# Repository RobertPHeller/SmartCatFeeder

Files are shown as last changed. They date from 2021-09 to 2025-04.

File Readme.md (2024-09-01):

# Smart Cat Feeder

A smart cat feeder, an "upgrade" from the [feeder on
Thingiverse.com](https://www.thingiverse.com/thing:8175), using an ESP32-S3
Dev board -- a more powerful processor. It will have a touch screen, and
provide a web server over WiFi. It will use a load cell to measure how full
the food bowl is, it will have a sensor to check when the food bin is low and
have a battery backup to operate in the event of a power failure, to insure
your cat will be fed when the power goes out.

[Adafruit Parts List](http://www.adafruit.com/wishlists/595396)
- [Adafruit TFT FeatherWing - 3.5" 480x320 Touchscreen for Feathers - V2 with TSC2007](https://www.adafruit.com/product/3651)
- [DC Motor + Stepper FeatherWing Add-on For All Feather Boards](https://www.adafruit.com/product/2927)
- [Adafruit VL6180X Time of Flight Distance Ranging Sensor (VL6180) - STEMMA QT](https://www.adafruit.com/product/3316)
- [Adafruit NAU7802 24-Bit ADC - STEMMA QT / Qwiic](https://www.adafruit.com/product/4538)
- [Adafruit PCF8523 Real Time Clock Breakout Board - STEMMA QT / Qwiic](https://www.adafruit.com/product/5189)
- [Strain Gauge Load Cell - 4 Wires - 1Kg](https://www.adafruit.com/product/4540)
- [Adafruit ESP32-S3 Feather with STEMMA QT / Qwiic - 8MB Flash No PSRAM](https://www.adafruit.com/product/5323)
- 2x [STEMMA QT / Qwiic JST SH 4-Pin Cable - 50mm Long](https://www.adafruit.com/product/4399)
- [STEMMA QT / Qwiic JST SH 4-pin Cable - 100mm Long](https://www.adafruit.com/product/4210)
- [Woven USB Cable with USB Type A to Right Angle USB Type C - Black 1 meter long](https://www.adafruit.com/product/5031)

DF Robot Parts list
- 2x [Turbo Metal Gear Worm Motor (12V 40RPM 8kg.cm)](https://www.dfrobot.com/product-1484.html)

Amazon Parts list
- [Van Ness Pets Lightweight Stainless Steel Cat Bowl, 8 OZ Food And Water Dish, Natural](https://www.amazon.com/Van-Ness-Lightweight-Dish-8-Ounce/dp/B00LM90GJI/)

Woodpeckers Crafts Parts List
- [1/8" x 24" x 48" Baltic Birch Sheets B/BB](https://woodpeckerscrafts.com/1-8-x-24-x-48-baltic-birch-sheets-b-bb/)
- 2x [1/4" x 12" Dowel](https://woodpeckerscrafts.com/1-4-x-12-dowel/)
- [1/2" x 12" Dowel Rod](https://woodpeckerscrafts.com/1-2-x-12-dowel-rod/)

Misc hardware
- 10 M3x6mm Allen head
- 7  M4x6mm Allen head
- 4  M6x12mm Allen head
- 4  M6 nuts
- 12 M2.5x6 flat head (counter sunk)
- 4  M2.5x12 flat head (counter sunk)
- 16 M2.5 nuts
- 4  M2.5x4 spacers
- 6  6-32x3/4" round head
- 7  6-32 nuts
- 4  #6x1/4 spacers (one metal, 3 plastic)
- small hinges
- magnetic cabinate door latch

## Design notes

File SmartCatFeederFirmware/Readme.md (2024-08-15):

# Smart Cat Feeder Firmware

Code for the Adafruit ESP32S3 Feather

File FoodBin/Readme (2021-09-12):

FreeCAD Python Scripts for the feed bin and framework.  Panels to be laser cut
from 1/8" plywood.

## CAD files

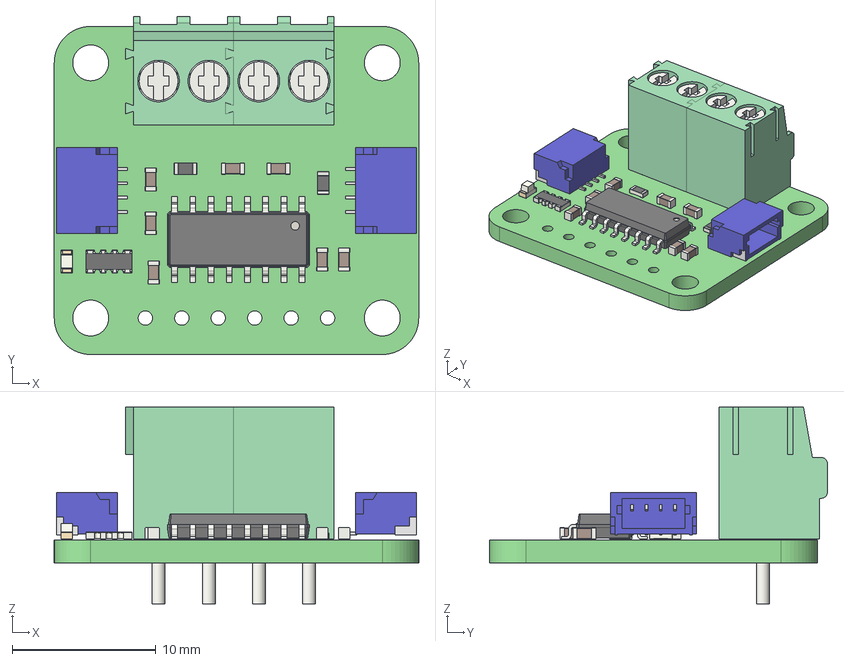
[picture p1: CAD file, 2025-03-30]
FoodBin/AdafruitNAU7802.step
25.4 x 23.6 x 13.7 mm
Adafruit NAU7802 Breakout PCB

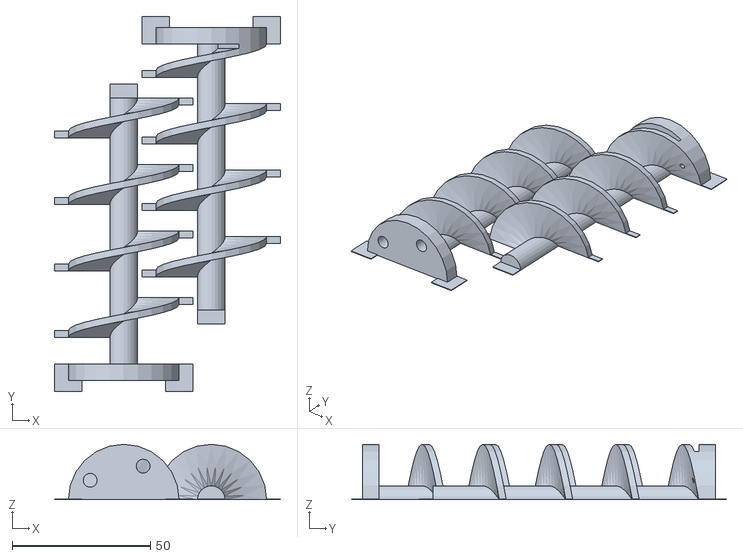
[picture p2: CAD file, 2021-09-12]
Auger_Drive_Screw_Conveyor/AugerWithCurlFlash.stl
81.6 x 135.4 x 20.0

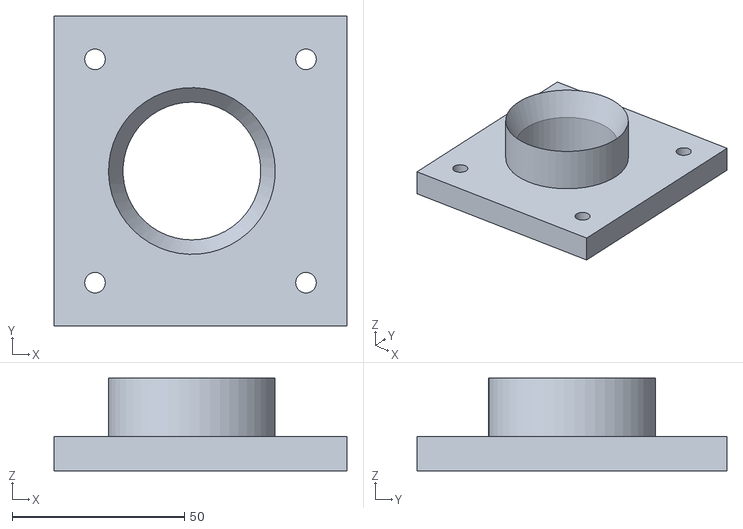
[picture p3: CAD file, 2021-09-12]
Auger_Drive_Screw_Conveyor/AugerMount.stl
85.0 x 90.0 x 27.0

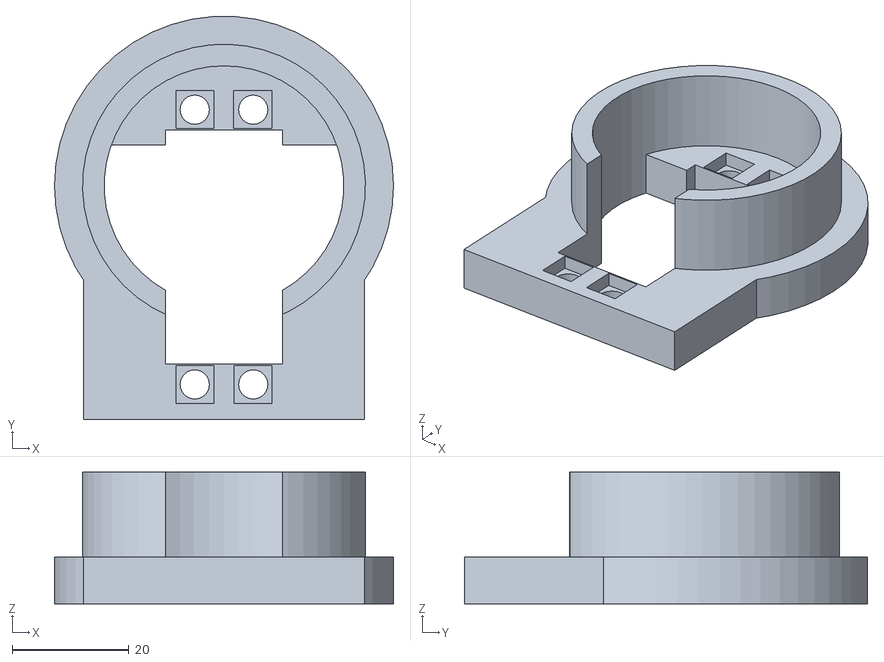
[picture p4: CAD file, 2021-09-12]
Auger_Drive_Screw_Conveyor/ServoMount.stl
58.0 x 68.9 x 22.5

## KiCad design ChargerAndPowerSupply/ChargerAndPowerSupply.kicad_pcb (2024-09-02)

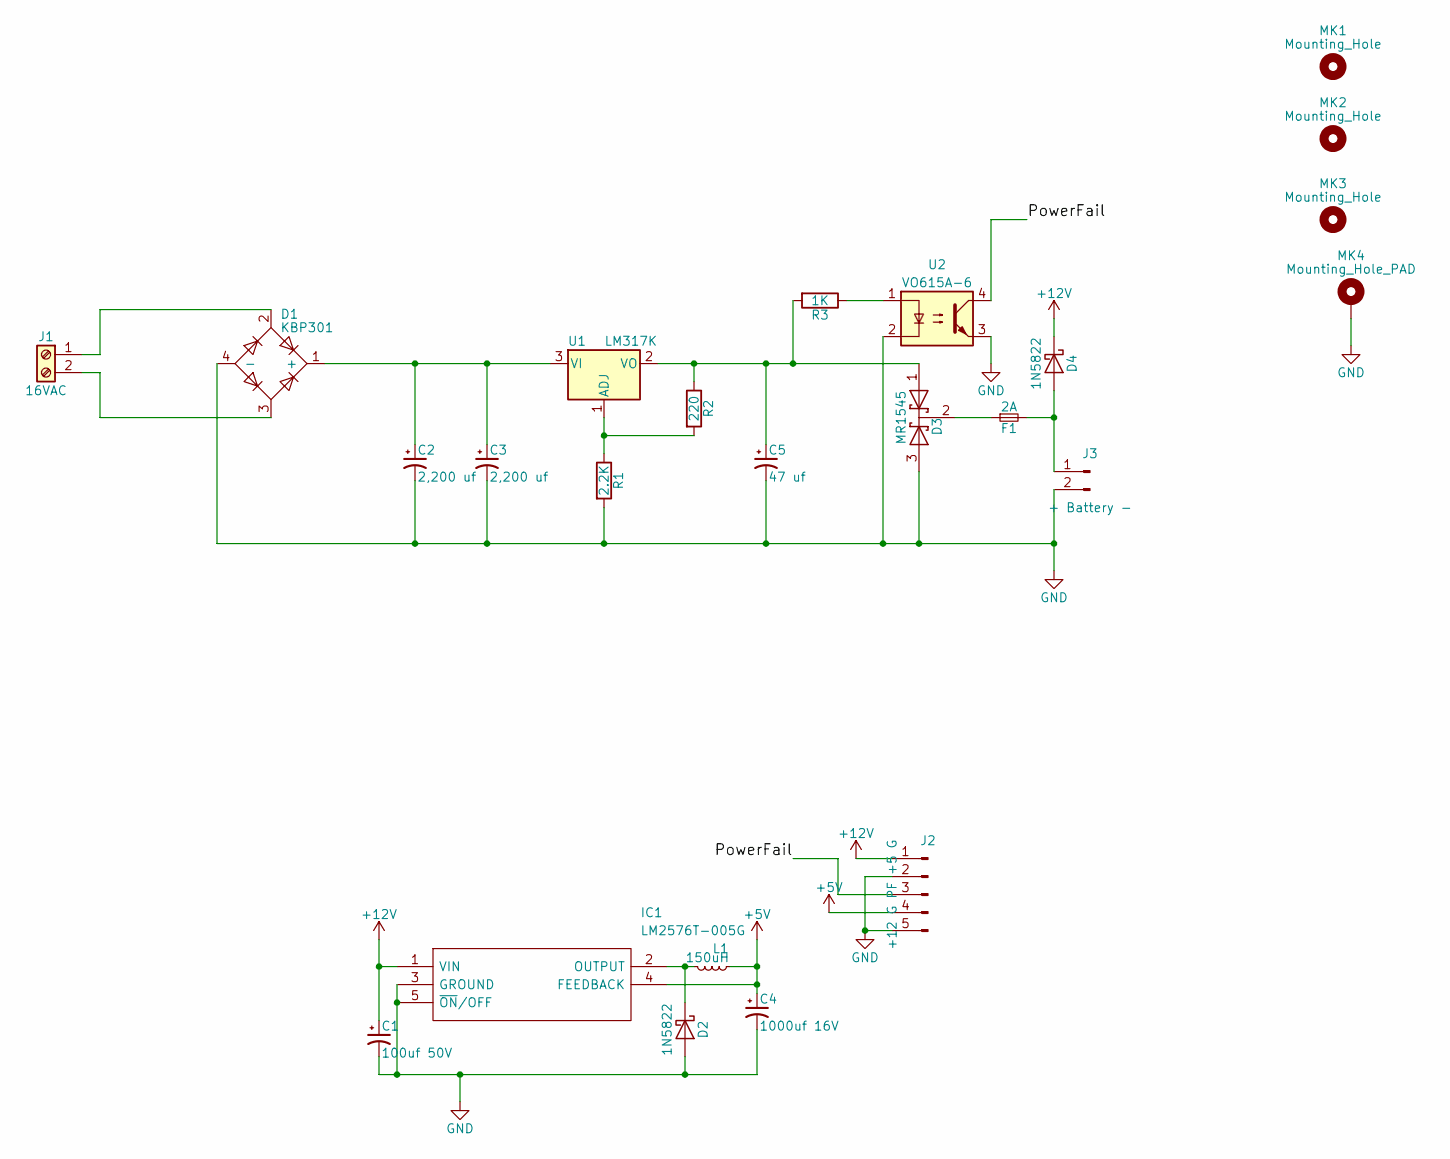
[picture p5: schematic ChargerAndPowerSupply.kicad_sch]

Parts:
C1: 100uf 50V; CP_Radial_D8.0mm_P5.00mm; Mouser Part Number 667-EEU-FR1H101B
C2, C3: 2,200 uf; CP_Radial_D16.0mm_P7.50mm; Mouser Part Number 140-REA222M1HBK1636P
C4: 1000uf 16V; CP_Radial_D10.0mm_P5.00mm; Mouser Part Number 667-EEU-FR1C102
C5: 47 uf; CP_Radial_D6.3mm_P2.50mm; Mouser Part Number 140-REA470M1HBK0611P
D1: KBP301; KBP301G; Mouser Part Number 905-KBP301
D2, D4: 1N5822; D_DO-201AD_P15.24mm_Horizontal
D3: MR1545; TO-220_Vertical
F1: 2A; MRT2; Mouser Part Number 530-MRT2
IC1: LM2576T-005G; TO-220-5_Pentawatt_Multiwatt-5_Vertical_StaggeredType1; Mouser2 Part Number 863-LM2576T-005G
J1: 16VAC; TerminalBlock_Pheonix_MKDS1.5-2pol; Mouser Part Numer 651-1017491
J2: +12 G PF +5 G; 26607050
J3: + Battery -; 26607020
L1: 150uH; L_Toroid_Vertical_L24.6mm_W15.5mm_P11.44mm_Pulse_KM-4; Mouser Part Number 673-PE-53113NL
MK1, MK2, MK3: Mounting_Hole; MountingHole_4.5mm
MK4: Mounting_Hole_PAD; MountingHole_4.5mm_Pad
R1: 2.2K; R_Axial_DIN0204_L3.6mm_D1.6mm_P7.62mm_Horizontal; Mouser Part Number 603-CFR-12JT-52-2K2
R2: 220; R_Axial_DIN0204_L3.6mm_D1.6mm_P7.62mm_Horizontal; Mouser Part Number 603-CFR-12JT-52-220R
R3: 1K; R_Axial_DIN0204_L3.6mm_D1.6mm_P7.62mm_Horizontal; Mouser Part Number 603-CFR-12JB-52-1K
U1: LM317K; TO-220_Vertical; Mouser Part Number LM317KCT
U2: VO615A-6; DIP-4_W7.62mm

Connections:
+5V: C4.1, IC1.4 (FEEDBACK), J2.4, L1.1
+12V: C1.1, D4.1 (K), IC1.1 (VIN), J2.1
/PowerFail: J2.3, U2.4
GND: C1.2, C2.2, C3.2, C4.2, C5.2, D1.4 (-), D2.2 (A), D3.3 (A), IC1.3 (GROUND), IC1.5 (~ON/OFF), J2.2, J2.5, J3.2, MK4.1, R1.2, U2.2, U2.3
unnamed: C2.1, C3.1, D1.1 (+), U1.3 (VI)
unnamed: C5.1, D3.1 (A), R2.1, R3.2, U1.2 (VO)
unnamed: D1.2, J1.1
unnamed: D1.3, J1.2
unnamed: D2.1 (K), IC1.2 (OUTPUT), L1.2
unnamed: D3.2 (K), F1.1
unnamed: D4.2 (A), F1.2, J3.1
unnamed: R1.1, R2.2, U1.1 (ADJ)
unnamed: R3.1, U2.1

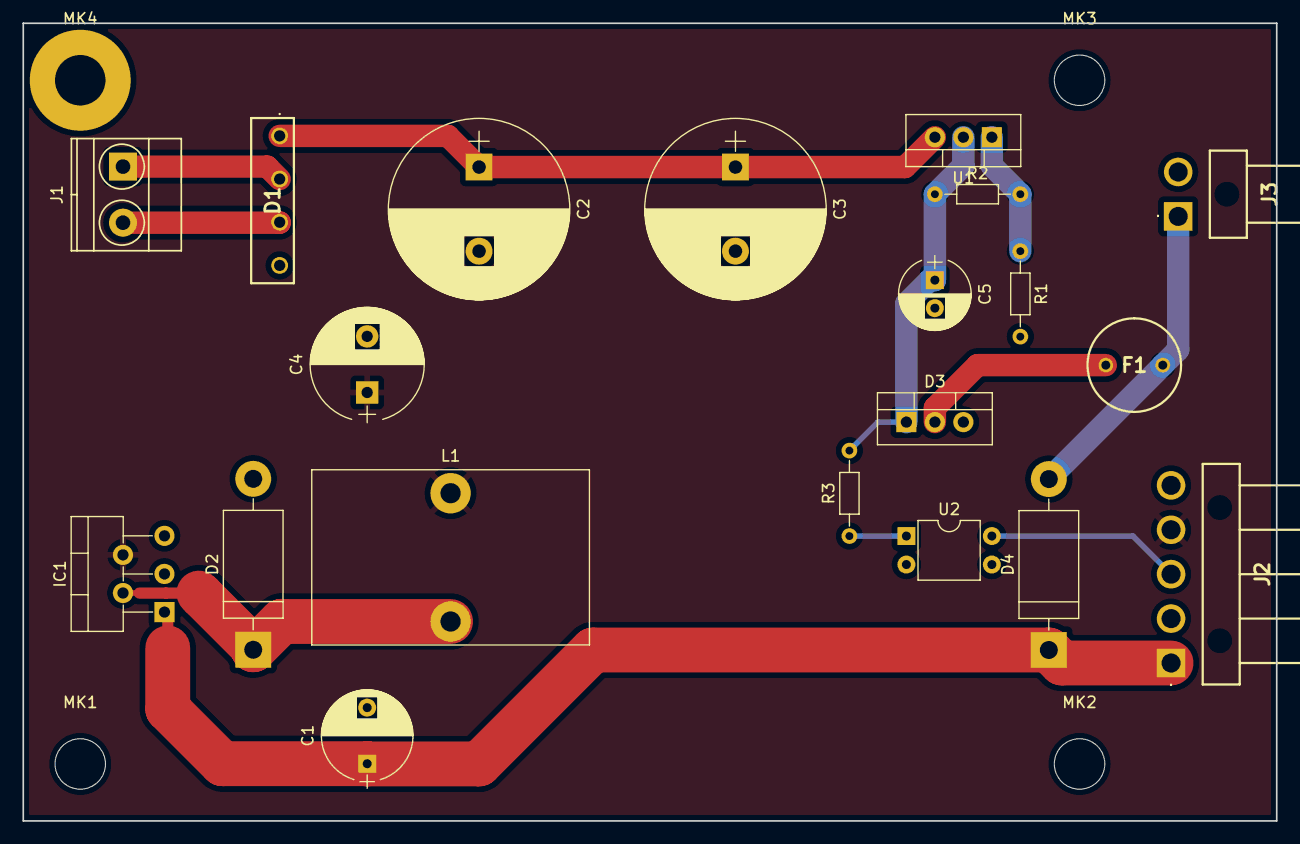
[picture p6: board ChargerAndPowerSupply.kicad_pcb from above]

Board: 2 copper layers, 111.8 x 71.1 mm, 24 parts (0 on the bottom side), 13 nets.

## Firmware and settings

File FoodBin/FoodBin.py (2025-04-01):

#*****************************************************************************
#
#  System        : 
#  Module        : 
#  Object Name   : $RCSfile$
#  Revision      : $Revision$
#  Date          : $Date$
#  Author        : $Author$
#  Created By    : Robert Heller
#  Created       : Sun Sep 12 20:13:56 2021
#  Last Modified : <250331.1602>
#
#  Description	
#
#  Notes
#
#  History
#	
#*****************************************************************************
#
#    Copyright (C) 2021  Robert Heller D/B/A Deepwoods Software
#			51 Locke Hill Road
#			Wendell, MA 01379-9728
#
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
# 
#
#*****************************************************************************


import FreeCAD as App
import Part, TechDraw, Mesh
from FreeCAD import Base

import os
import sys
sys.path.append(os.path.dirname(__file__))

import AugerMount
import Pi4
import ChargerPS
import Adafruit
import DFRobotGearMotor

import csv

class WoodBOM(object):
    _woodBOM = dict()
    @classmethod
    def AddPiece(cls,width,height,length):
        key = (width,height,length)
        if key in cls._woodBOM:
            cls._woodBOM[key] += 1
        else:
            cls._woodBOM[key] = 1
    @staticmethod
    def _normPartSizeMM(t):
        return ("%.3fx%.3fx%.3f" % t)
    @staticmethod
    def _inch(mm):
        return mm / 25.4
    @staticmethod
    def _normPartSizeIN(t):
        X, Y, Z = t
        return ("%.4fx%.4fx%.4f" % (WoodBOM._inch(X), WoodBOM._inch(Y), WoodBOM._inch(Z)))
    _units = 'in'
    @classmethod
    def SetUnits(cls,units):
        if units == 'in' or units == 'mm':
            cls._units = units
        else:
            raise RuntimeError("Unsupport units!")
    @classmethod
    def GetUnits(cls):
        return cls._units
    @classmethod
    def _normPartSize(cls,t):
        if cls._units == 'in':
            return WoodBOM._normPartSizeIN(t)
        elif cls._units == 'mm':
            return WoodBOM._normPartSizeMM(t)
        else:
            raise RuntimeError("Unsupport units!")
    @classmethod
    def ListCuts(cls,filename):
        keys = list(cls._woodBOM.keys())
        keys.sort()
        f = open(filename,"w")
        w = csv.writer(f)
        w.writerow([("Size (%s)" % cls._units),"Count"])
        for key in keys:
            w.writerow([cls._normPartSize(key),cls._woodBOM[key]])
        f.close()
    def __init__(self):
        raise RuntimeError("No Instances allowed for WoodBOM!")
        

class HalfByHalf(object):
    __Width = .5 * 25.4
    @classmethod
    def ZBeam(cls,origin,length):
        if not isinstance(origin,Base.Vector):
            raise RuntimeError("origin is not a Vector!")
        beam = Part.makePlane(cls.__Width,cls.__Width,origin,\
                              Base.Vector(0,0,1))\
                  .extrude(Base.Vector(0,0,length))
        bb = beam.BoundBox
        WoodBOM.AddPiece(bb.XLength,bb.YLength,bb.ZLength)
        return beam
    @classmethod
    def XBeam(cls,origin,length):
        if not isinstance(origin,Base.Vector):
            raise RuntimeError("origin is not a Vector!")
        beam = Part.makePlane(cls.__Width,cls.__Width,origin,\
                              Base.Vector(1,0,0))\
                  .extrude(Base.Vector(length,0,0))
        bb = beam.BoundBox
        WoodBOM.AddPiece(bb.YLength,bb.ZLength,bb.XLength)
        return beam
    @classmethod
    def YBeam(cls,origin,length):
        if not isinstance(origin,Base.Vector):
            raise RuntimeError("origin is not a Vector!")
        beam = Part.makePlane(cls.__Width,cls.__Width,origin,\
                              Base.Vector(0,1,0))\
                  .extrude(Base.Vector(0,length,0))
        bb = beam.BoundBox
        WoodBOM.AddPiece(bb.ZLength,bb.XLength,bb.YLength)
        return beam

            
import math

def radians(degrees):
    return (degrees/180)*math.pi

class Agitator(object):
    __AgitatorDiskDiameter = 50.8 # 2"
    __DiskThickness = .125 * 25.4
    __CenterDowelDiameter = 12.5 # 1/2"
    __OuterDowelDiameter = 6.25  # 1/4"
    __OuterDowelRadius   = .75*25.4
    __OuterDowelStartAngle = 0
    __OuterDowelDeltaAngle = 90
    __AgitatorLength = 4.125 * 25.4
    __AgitatorDiskSpacing = (4 / 3)*25.4
    __CenterDowelLength = 5 * 25.4
    __FrontDowelHoleDiameter = 13.5
    __Color = tuple([210.0/255.0,180.0/255.0,140.0/255.0])
    def __init__(self,name,origin):
        self.name = name
        if not isinstance(origin,Base.Vector):
            raise RuntimeError("origin is not a Vector!")
        self.origin = origin
        self.center = Part.Face(Part.Wire(Part.makeCircle(self.__CenterDowelDiameter/2,\
                                                          origin,
                                                          Base.Vector(0,1,0))))\
                            .extrude(Base.Vector(0,-self.__CenterDowelLength,0))
        self.outerDowels = list()
        for i in range(0,4):
            dang = self.__OuterDowelDeltaAngle*i
            hX = self.__OuterDowelRadius * \
                        math.cos(radians(self.__OuterDowelStartAngle+dang))
            hZ = self.__OuterDowelRadius * \
                        math.sin(radians(self.__OuterDowelStartAngle+dang))
            dowelOrigin = origin.add(Base.Vector(hX,0,hZ))
            self.outerDowels.append(\
                Part.Face(Part.Wire(Part.makeCircle(self.__OuterDowelDiameter/2,\
                                                    dowelOrigin,\
                                                    Base.Vector(0,1,0))))\
                            .extrude(Base.Vector(0,-self.__AgitatorLength,0)))
        self.disks = list()
        for i in range(0,4):
            diskOrigin = origin.add(Base.Vector(0,-(i*self.__AgitatorDiskSpacing),0))
            disk = Part.Face(Part.Wire(Part.makeCircle(self.__AgitatorDiskDiameter/2,\
                                                       diskOrigin,\
                                                       Base.Vector(0,1,0))))\
                             .extrude(Base.Vector(0,-self.__DiskThickness,0))
            if i == 0:
                disk = DFRobotGearMotor.AgitatorMountPlate.MountYHoleRing(disk,diskOrigin,self.__DiskThickness)
            disk = disk.cut(self.center)
            for j in range(0,4):
                disk = disk.cut(self.outerDowels[j])
            self.disks.append(disk)
    def FrontHole(self,Y,DeltaY):
        hOrigin = Base.Vector(self.origin.x,Y,self.origin.z)
        return Part.Face(Part.Wire(Part.makeCircle(self.__FrontDowelHoleDiameter/2,\
                                                          hOrigin,
                                                          Base.Vector(0,1,0))))\
                            .extrude(Base.Vector(0,DeltaY,0))
        
    def show(self,doc=None):
        if doc==None:
            doc = App.activeDocument()
        obj = doc.addObject("Part::Feature",self.name+"_center")
        obj.Shape = self.center
        obj.Label=self.name+"_center"
        obj.ViewObject.ShapeColor=self.__Color
        for i in range(0,4):
            name="_outerDowel%d"%(i+1)
            obj = doc.addObject("Part::Feature",self.name+name)
            obj.Shape = self.outerDowels[i]
            obj.Label=self.name+name
            obj.ViewObject.ShapeColor=self.__Color
        for i in range(0,4):
            name="_disk%d"%(i+1)
            obj = doc.addObject("Part::Feature",self.name+name)
            obj.Shape = self.disks[i]
            obj.Label=self.name+name
            obj.ViewObject.ShapeColor=self.__Color

class Bowl(object):
    __OuterDiameter = 5*25.4
    __BowlLargeDiameter = 4.65*25.4
    __BowlBottomDiameter = 4.0*25.4
    __RimSize       = .25*25.4
    __Height        = 1.25*25.4
    __Thickness     = 1.5
    __Color = tuple([0.8,0.8,0.8])
    def __init__(self,name,origin):
        self.name = name
        if not isinstance(origin,Base.Vector):
            raise RuntimeError("origin is not a Vector!")
        self.origin = origin
        outerrad = self.__OuterDiameter/2
        rim = Part.Face(Part.Wire(Part.makeCircle(outerrad,origin.add(Base.Vector(0,0,self.__Height-self.__Thickness))))).extrude(Base.Vector(0,0,self.__Thickness))
        rim = rim.cut(Part.Face(Part.Wire(Part.makeCircle(outerrad-self.__RimSize,origin.add(Base.Vector(0,0,self.__Height-self.__Thickness))))).extrude(Base.Vector(0,0,self.__Thickness)))
        body = Part.makeCone(self.__BowlBottomDiameter/2,\
                             self.__BowlLargeDiameter/2,\
                             self.__Height-self.__Thickness,origin,Base.Vector(0,0,1))  
        inside = Part.makeCone((self.__BowlBottomDiameter/2)-self.__Thickness,\
                               (self.__BowlLargeDiameter/2)-self.__Thickness,\
                               self.__Height-2*self.__Thickness,\
                               origin.add(Base.Vector(0,0,self.__Thickness)),\
                               Base.Vector(0,0,1))
        body = body.cut(inside)
        self.bowl = rim.fuse(body)
    def CutHole(self,part):
        b = Part.Face(Part.Wire(Part.makeCircle((self.__BowlLargeDiameter/2)+self.__Thickness,self.origin))).extrude(Base.Vector(0,0,self.__Height))
        return part.cut(b)
    def show(self,doc=None):
        if doc==None:
            doc = App.activeDocument()
        obj = doc.addObject("Part::Feature",self.name)
        obj.Shape = self.bowl
        obj.Label=self.name
        obj.ViewObject.ShapeColor=self.__Color

class Tee(object):
    __OuterDiameter = (2.25*25.4)
    __InnerDiameter = (1.875*25.4)
    __Length        = (4.125*25.4)
    @classmethod
    def Length(cls):
        return cls.__Length
    __Rise          = (2.5*25.4)
    @classmethod
    def Rise(cls):
        return cls.__Rise
    __Front         = (2.5*25.4)
    @classmethod
    def Front(cls):
        return cls.__Front
    __Color         = tuple([1.0,1.0,1.0])
    def __init__(self,name,origin):
        self.name = name
        if not isinstance(origin,Base.Vector):
            raise RuntimeError("origin is not a Vector!")
        self.origin = origin
        TNorm = Base.Vector(0,1,0)
        RNorm = Base.Vector(0,0,1)
        TBody = Part.Face(Part.Wire(Part.makeCircle(self.__OuterDiameter/2.0,\
                                                    origin,\
                                                    TNorm)))\
                          .extrude(Base.Vector(0,self.__Length,0))
        Rise = Part.Face(Part.Wire(Part.makeCircle(self.__OuterDiameter/2.0,\
                                                   origin.add(Base.Vector(0,self.__Front,0)),\
                                                   RNorm)))\
                           .extrude(Base.Vector(0,0,self.__Rise))
        Rise = Rise.cut(TBody)
        TBody = TBody.fuse(Rise)
        TBody = TBody.cut(\
                Part.Face(Part.Wire(Part.makeCircle(self.__InnerDiameter/2.0,\
                                                    origin.add(Base.Vector(0,self.__Front,0)),\
                                                   RNorm)))\
                           .extrude(Base.Vector(0,0,self.__Rise)))
        TBody = TBody.cut(\
                Part.Face(Part.Wire(Part.makeCircle(self.__InnerDiameter/2.0,\
                                                    origin,\
                                                    TNorm)))\
                           .extrude(Base.Vector(0,self.__Length,0)))
        self.body = TBody
    def show(self,doc=None):
        if doc==None:
            doc = App.activeDocument()
        obj = doc.addObject("Part::Feature",self.name)
        obj.Shape = self.body
        obj.Label=self.name
        obj.ViewObject.ShapeColor=self.__Color
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

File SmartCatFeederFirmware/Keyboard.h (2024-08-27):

// -!- c++ -!- //////////////////////////////////////////////////////////////
//
//  System        : 
//  Module        : 
//  Object Name   : $RCSfile$
//  Revision      : $Revision$
//  Date          : $Date$
//  Author        : $Author$
//  Created By    : Robert Heller
//  Created       : Sat Aug 24 21:11:51 2024
//  Last Modified : <240827.1517>
//
//  Description	
//
//  Notes
//
//  History
//	
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
#ifndef __KEYBOARD_H
#define __KEYBOARD_H

#include <Adafruit_GFX.h>
#include "Display.h"

#include <stdio.h>

#define HASSERT(x) if (!(x)) \
{ \
    char buffer[256];\
    snprintf(buffer,sizeof(buffer),"Assertion failed in file " __FILE__ " line %d: assert(%s)", __LINE__, #x); \
    Serial.println(buffer);\
    while(1) delay(100);\
}


namespace Keyboard {

class Keyboard
{
public:
    Keyboard() : mode_(Off){}
    ~Keyboard() {}
    void start();
    void end();
    char KeyPressed();
private:
    static constexpr uint8_t Keys_ = 50;
    static constexpr uint8_t KeysRowStride_ = 10;
    static constexpr uint8_t KeyRowHeight_ = 32;
    static constexpr uint8_t KeyColumnWidth_ = 24;
    static constexpr uint16_t KOrigX_ = 120;
    static constexpr uint16_t KOrigY_ = 160;
    static constexpr uint16_t KWidth_ = KeysRowStride_*KeyColumnWidth_;
    static constexpr uint16_t KHeight_ = KeyRowHeight_*(Keys_/KeysRowStride_);
    typedef enum {Off=0, LowerAlnum, UpperAlnum, Special} KeyMode;
    void SetMode(KeyMode mode) {mode_ = mode;}
    typedef enum {blank=0, shift, return_l, return_r, delete_l, delete_r, 
        special, spacebar_l, spacebar_m, spacebar_r, alnum} IconId;
    typedef struct keyCell {
        int16_t col;
        int16_t row;
        uint8_t ischar:1;
        uint8_t newmode:2;
        uint8_t iconid:6;
        unsigned char c;
    } KeyCell;
    KeyMode mode_;
    void drawkeyboard_();
    const KeyCell *getTouch(uint16_t x, uint16_t y);
    uint8_t key_currstate[Keys_], key_laststate[Keys_];
    bool keyJustPressed(uint8_t i)
    {
        HASSERT(i < Keys_);
        return (key_currstate[i] && !key_laststate[i]);
    }
    bool keyJustReleased(uint8_t i)
    {
        HASSERT(i < Keys_);
        return  (!key_currstate[i] && key_laststate[i]);
    }
    void keyPress(uint8_t i, bool p)
    {
        HASSERT(i < Keys_);
        key_laststate[i] = key_currstate[i];
        key_currstate[i] = p;
    }
    bool keyIsPressed(uint8_t i)
    {
        HASSERT(i < Keys_); 
        return key_currstate[i];
    }
    static constexpr const KeyCell LowerAlnum_[Keys_] = {
        {0,0,1,LowerAlnum,blank,'1'},
        {1,0,1,LowerAlnum,blank,'2'},
        {2,0,1,LowerAlnum,blank,'3'},
        {3,0,1,LowerAlnum,blank,'4'},
        {4,0,1,LowerAlnum,blank,'5'},
        {5,0,1,LowerAlnum,blank,'6'},
        {6,0,1,LowerAlnum,blank,'7'},
        {7,0,1,LowerAlnum,blank,'8'},
        {8,0,1,LowerAlnum,blank,'9'},
        {9,0,1,LowerAlnum,blank,'0'},
        {0,1,1,LowerAlnum,blank,'q'},
        {1,1,1,LowerAlnum,blank,'w'},
        {2,1,1,LowerAlnum,blank,'e'},
        {3,1,1,LowerAlnum,blank,'r'},
        {4,1,1,LowerAlnum,blank,'t'},
        {5,1,1,LowerAlnum,blank,'y'},
        {6,1,1,LowerAlnum,blank,'u'},
        {7,1,1,LowerAlnum,blank,'i'},
        {8,1,1,LowerAlnum,blank,'o'},
        {9,1,1,LowerAlnum,blank,'p'},
        {0,2,0,UpperAlnum,shift,'\0'},
        {1,2,1,LowerAlnum,blank,'a'},
        {2,2,1,LowerAlnum,blank,'s'},
        {3,2,1,LowerAlnum,blank,'d'},
        {4,2,1,LowerAlnum,blank,'f'},
        {5,2,1,LowerAlnum,blank,'g'},
        {6,2,1,LowerAlnum,blank,'h'},
        {7,2,1,LowerAlnum,blank,'j'},
        {8,2,1,LowerAlnum,blank,'k'},
        {9,2,1,LowerAlnum,blank,'l'},
        {0,3,0,Special,special,'\0'},
        {1,3,1,LowerAlnum,blank,'z'},
        {2,3,1,LowerAlnum,blank,'x'},
        {3,3,1,LowerAlnum,blank,'c'},
        {4,3,1,LowerAlnum,blank,'v'},
        {5,3,1,LowerAlnum,blank,'b'},
        {6,3,1,LowerAlnum,blank,'n'},
        {7,3,1,LowerAlnum,blank,'m'},
        {8,3,1,LowerAlnum,return_l,'\r'},
        {9,3,1,LowerAlnum,return_r,'\r'},
        {0,4,1,LowerAlnum,blank,'.'},
        {1,4,1,LowerAlnum,blank,','},
        {2,4,1,LowerAlnum,spacebar_l,' '},
        {3,4,1,LowerAlnum,spacebar_m,' '},
        {4,4,1,LowerAlnum,spacebar_m,' '},
        {5,4,1,LowerAlnum,spacebar_m,' '},
        {6,4,1,LowerAlnum,spacebar_m,' '},
        {7,4,1,LowerAlnum,spacebar_r,' '},
        {8,4,1,LowerAlnum,delete_l,'\b'},
        {9,4,1,LowerAlnum,delete_r,'\b'}
    };
    static constexpr const KeyCell UpperAlnum_[Keys_] = {
        {0,0,1,LowerAlnum,blank,'1'},
        {1,0,1,LowerAlnum,blank,'2'},
        {2,0,1,LowerAlnum,blank,'3'},
        {3,0,1,LowerAlnum,blank,'4'},
        {4,0,1,LowerAlnum,blank,'5'},
        {5,0,1,LowerAlnum,blank,'6'},
        {6,0,1,LowerAlnum,blank,'7'},
        {7,0,1,LowerAlnum,blank,'8'},
        {8,0,1,LowerAlnum,blank,'9'},
        {9,0,1,LowerAlnum,blank,'0'},
        {0,1,1,LowerAlnum,blank,'Q'},
        {1,1,1,LowerAlnum,blank,'W'},
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

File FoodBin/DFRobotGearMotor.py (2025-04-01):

#*****************************************************************************
#
#  System        : 
#  Module        : 
#  Object Name   : $RCSfile$
#  Revision      : $Revision$
#  Date          : $Date$
#  Author        : $Author$
#  Created By    : Robert Heller
#  Created       : Sun Aug 18 11:37:13 2024
#  Last Modified : <250331.1546>
#
#  Description	
#
#  Notes
#
#  History
#	
#*****************************************************************************
#
#    Copyright (C) 2024  Robert Heller D/B/A Deepwoods Software
#			51 Locke Hill Road
#			Wendell, MA 01379-9728
#
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
# 
#
#*****************************************************************************


import FreeCAD as App
import Part, TechDraw
from FreeCAD import Base
import Mesh

import os
import sys
sys.path.append(os.path.dirname(__file__))

class DFRobotGearMotor(object):
    GearBoxHeight = 46
    GearBoxWidth  = 32
    GearBoxDepth  = 25.2-2.0
    GearBoxSpacers = 2.0
    MotorHeight   = 30.8
    MotorDiameter = 24.4
    MotorCenterXOff = 32-12.2
    MotorCenterYOff = 24.2-13.2
    ShaftDiameter = 6
    ShaftDFlat    = 5.4
    ShaftDFlatLength = 12
    ShaftClearHole = 6.5
    ShaftLength   = 18.5
    ShaftX        = 16
    ShaftZ        = 46-(6+9)
    @classmethod
    def ShaftY(cls):
        return cls.ShaftZ
    ShaftSpacerDia = 12 # Guess 
    MountingHoleX1 = (32-18)/2
    MountingHoleX2 = 32-((32-18)/2)
    MountingHoleZ1 = 7
    @classmethod
    def MountingHoleY1(cls):
        return cls.MountingHoleZ1
    MountingHoleZ2 = 46-6
    @classmethod
    def MountingHoleY2(cls):
        return cls.MountingHoleZ2
    MountingHoleDia = 3.6
    MountingHoleSpacerDia = 8 # Guess
    @classmethod
    def CutShaftZ(cls,origin,part,length):
        if not isinstance(origin,Base.Vector):
            raise RuntimeError("origin is not a Vector")
        if not isinstance(part,Part.Shape):
            raise RuntimeError("part is not a Shape")
        shaft = Part.Face(Part.Wire(Part.makeCircle(cls.ShaftDiameter/2.0,origin,Base.Vector(0,0,1)))).extrude(Base.Vector(0,0,length))
        d = Part.makePlane(length,cls.ShaftDiameter,\
                           origin.add(Base.Vector(-cls.ShaftDiameter/2.0,\
                                                  cls.ShaftDFlat-(cls.ShaftDiameter/2),\
                                                  0)),\
                           Base.Vector(0,1,0)).extrude(Base.Vector(0,cls.ShaftDiameter-cls.ShaftDFlat,0))
        shaft = shaft.cut(d)
        return part.cut(shaft)
    @classmethod
    def OriginFromShaftHole(cls,shaftOrigin):
        if not isinstance(shaftOrigin,Base.Vector):
            raise RuntimeError("shaftOrigin is not a Vector")
        return shaftOrigin.add(Base.Vector(-cls.ShaftX,\
                                           -(cls.GearBoxDepth+cls.GearBoxSpacers),\
                                           -(cls.ShaftZ+cls.MotorHeight)))
    def __init__(self,name,origin):
        self.name = name
        if not isinstance(origin,Base.Vector):
            raise RuntimeError("origin is not a Vector")
        self.origin = origin
        self.motor = Part.Face(Part.Wire(Part.makeCircle(self.MotorDiameter/2.0,\
                                         origin.add(Base.Vector(self.MotorCenterXOff,\
                                                                self.MotorCenterYOff,\
                                                                0)),\
                                         Base.Vector(0,0,1))))\
                            .extrude(Base.Vector(0,0,self.MotorHeight))
        gearboxOrigin = origin.add(Base.Vector(0,0,self.MotorHeight))
        self.gearbox = Part.makePlane(self.GearBoxWidth,self.GearBoxDepth,\
                                      gearboxOrigin)\
                           .extrude(Base.Vector(0,0,self.GearBoxHeight))
        self.MountingHoles = list()
        self.MountingHoles.append(gearboxOrigin.add(Base.Vector(self.MountingHoleX1,\
                                                                0,\
                                                                self.MountingHoleZ1)))
        self.MountingHoles.append(gearboxOrigin.add(Base.Vector(self.MountingHoleX2,\
                                                                0,\
                                                                self.MountingHoleZ1)))
        self.MountingHoles.append(gearboxOrigin.add(Base.Vector(self.MountingHoleX1,\
                                                                0,\
                                                                self.MountingHoleZ2)))
        self.MountingHoles.append(gearboxOrigin.add(Base.Vector(self.MountingHoleX2,\
                                                                0,\
                                                                self.MountingHoleZ2)))
        for i in range(0,4):
            hspace = Part.Face(Part.Wire(Part.makeCircle(self.MountingHoleSpacerDia/2.0,\
                                                         self.MountingHoles[i],\
                                                         Base.Vector(0,1,0))))\
                        .extrude(Base.Vector(0,-self.GearBoxSpacers,0))
            self.gearbox = self.gearbox.fuse(hspace)
        self.shaftOrigin = gearboxOrigin.add(Base.Vector(self.ShaftX,0,self.ShaftZ))
        self.shaft = Part.Face(Part.Wire(Part.makeCircle(self.ShaftDiameter/2.0,\
                                                         self.shaftOrigin,\
                                                         Base.Vector(0,1,0))))\
                         .extrude(Base.Vector(0,-self.ShaftLength))
        d = Part.makePlane(self.ShaftDiameter,self.ShaftDFlatLength,\
                           self.shaftOrigin.add(Base.Vector(-self.ShaftDiameter/2,\
                         -self.ShaftLength,\
                                                self.ShaftDFlat-(self.ShaftDiameter/2))))\
                       .extrude(Base.Vector(0,0,self.ShaftDiameter-self.ShaftDFlat))
        #self.d = d
        self.shaft = self.shaft.cut(d)
        sspace = Part.Face(Part.Wire(Part.makeCircle(self.ShaftSpacerDia/2.0,\
                                                         self.shaftOrigin,\
                                                         Base.Vector(0,1,0))))\
                         .extrude(Base.Vector(0,-self.GearBoxSpacers))
        self.gearbox = self.gearbox.fuse(sspace)
    def MountingHole(self,i,Y,YDelta):
        xhole = self.MountingHoles[i]
        HoleOrigin = Base.Vector(xhole.x,Y,xhole.z)
        hole = Part.Face(Part.Wire(Part.makeCircle(self.MountingHoleDia/2,HoleOrigin,Base.Vector(0,1,0))))\
                    .extrude(Base.Vector(0,YDelta,0))
        return hole
    def ShaftHole(self,Y,YDelta):
        HoleOrigin = Base.Vector(self.shaftOrigin.x,Y,self.shaftOrigin.z)
        hole = Part.Face(Part.Wire(Part.makeCircle(self.ShaftClearHole/2,HoleOrigin,Base.Vector(0,1,0))))\
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

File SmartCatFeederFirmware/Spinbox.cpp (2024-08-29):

// -!- C++ -!- //////////////////////////////////////////////////////////////
//
//  System        : 
//  Module        : 
//  Object Name   : $RCSfile$
//  Revision      : $Revision$
//  Date          : $Date$
//  Author        : $Author$
//  Created By    : Robert Heller
//  Created       : Wed Aug 28 14:59:30 2024
//  Last Modified : <240828.2205>
//
//  Description	
//
//  Notes
//
//  History
//	
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
static const char rcsid[] = "@(#) : $Id$";


#include <Arduino.h>
#include <stdio.h>
#include <Adafruit_GFX.h>
#include "Spinbox.h"
#include "BackgroundTask.h"

#include "incr.xbm.h"
#include "decr.xbm.h"

#ifndef min
#define min(a, b) (((a) < (b)) ? (a) : (b))
#endif

Spinbox::Spinbox(Adafruit_GFX *gfx, int16_t x, int16_t y, uint16_t outline, 
                 uint16_t fill,uint16_t textcolor, int16_t minv, int16_t maxv, 
                 const char *fmt)
      : _gfx(gfx)
, _x1(x)
, _y1(y)
, _incr_w(incr_width)
, _incr_h(incr_height)
, _decr_w(decr_width)
, _decr_h(decr_height)
, _textsize_x(5)
, _textsize_y(5)
, _outlinecolor(outline)
, _fillcolor(fill)
, _textcolor(textcolor)
, _minVal(minv)
, _maxVal(maxv)
{
    char tempbuffer[20];
    int16_t tempx, tempy;
    uint16_t tempw, temph;
    _hh = _incr_h+_decr_h;
    strncpy(_format,fmt,9);
    _format[9] = '\0';
    snprintf(tempbuffer,sizeof(tempbuffer),_format,_minVal);
    _gfx->setTextSize(_textsize_x,_textsize_y);
    _gfx->getTextBounds(tempbuffer,0,0,&tempx,&tempy,&tempw,&temph);
    tempw += 4;
    temph += 4;
    _ww = tempw+incr_width;
    if (_ww < tempw+decr_width) _ww = tempw+decr_width;
    if (_hh < temph) _hh = temph;
    snprintf(tempbuffer,sizeof(tempbuffer),_format,_maxVal);
    _gfx->getTextBounds(tempbuffer,0,0,&tempx,&tempy,&tempw,&temph);
    tempw += 4;
    temph += 4;
    if (_ww < tempw+incr_width+4) _ww = tempw+incr_width;
    if (_ww < tempw+decr_width) _ww = tempw+decr_width;
    if (_hh < temph) _hh = temph;
    _incr_y1 = _y1;
    _decr_y1 = (_y1+_hh)-decr_height;
    int16_t right = _x1 + _ww;
    _incr_x1 = right-incr_width;
    _decr_x1 = right-decr_width;
    if (_decr_x1 < _incr_x1) _incr_x1 = _decr_x1;
    if (_incr_x1 < _decr_x1) _decr_x1 = _incr_x1;
}

void Spinbox::drawBox(int16_t value)
{
    char buffer[20];
    _value = value;
    snprintf(buffer,sizeof(buffer),_format,_value);
    int w = _ww - max(incr_width,decr_width);
    uint8_t r = min(w, _hh) / 4; // Corner radius
    _gfx->fillRoundRect(_x1, _y1, w, _hh,  r, _fillcolor);
    _gfx->drawRoundRect(_x1, _y1, w, _hh,  r, _outlinecolor);
    _gfx->setCursor(_x1 + (w / 2) - (strlen(buffer) * 3 * _textsize_x),
                    _y1 + (_hh / 2) - (4 * _textsize_y));
    _gfx->setTextColor(_textcolor);
    _gfx->setTextSize(_textsize_x, _textsize_y);
    _gfx->print(buffer);
    _gfx->drawXBitmap(_incr_x1,_incr_y1,incr_bits,incr_width,incr_height,
                      _textcolor);
    _gfx->drawXBitmap(_decr_x1,_decr_y1,decr_bits,decr_width,decr_height,
                      _textcolor);
}

bool Spinbox::incrContains(int16_t x, int16_t y) 
{
    return ((x >= _incr_x1) && (x < (int16_t)(_incr_x1 + _incr_w)) && 
            (y >= _incr_y1) && (y < (int16_t)(_incr_y1 + _incr_h)));
}

bool Spinbox::decrContains(int16_t x, int16_t y) 
{
    return ((x >= _decr_x1) && (x < (int16_t)(_decr_x1 + _decr_w)) && 
            (y >= _decr_y1) && (y < (int16_t)(_decr_y1 + _decr_h)));
}

bool Spinbox::incrJustPressed() 
{ 
    return (incr_currstate && !incr_laststate); 
}

bool Spinbox::decrJustPressed() 
{ 
    return (decr_currstate && !decr_laststate); 
}

bool Spinbox::incrJustReleased() 
{ 
    return (!incr_currstate && incr_laststate); 
} 

bool Spinbox::decrJustReleased() 
{ 
    return (!decr_currstate && decr_laststate); 
} 

void Spinbox::incr()
{
    if (_value < _maxVal) 
    {
        _value++;
        char buffer[20];
        snprintf(buffer,sizeof(buffer),_format,_value);
        int w = _ww - max(incr_width,decr_width);
        _gfx->setCursor(_x1 + (w / 2) - (strlen(buffer) * 3 * _textsize_x),
                        _y1 + (_hh / 2) - (4 * _textsize_y));
        _gfx->setTextColor(_textcolor);
        _gfx->setTextSize(_textsize_x, _textsize_y);
        _gfx->print(buffer);
    }
}

void Spinbox::decr()
{
    if (_value > _minVal) 
    {
        _value--;
        char buffer[20];
        snprintf(buffer,sizeof(buffer),_format,_value);
        int w = _ww - max(incr_width,decr_width);
        _gfx->setCursor(_x1 + (w / 2) - (strlen(buffer) * 3 * _textsize_x),
                        _y1 + (_hh / 2) - (4 * _textsize_y));
        _gfx->setTextColor(_textcolor);
        _gfx->setTextSize(_textsize_x, _textsize_y);
        _gfx->print(buffer);
    }
}
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

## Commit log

2021-09-12 Add initial files
    [AugerMount.stl, AugerWithCurlFlash.stl, LaserFeedBinEmptyCheck.kicad_pcb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]
2021-09-13 Completing the feed bin, added holes for auger mount.
2021-09-14 Completed Laser Diode drive circuit.
    [LaserFeedBinEmptyCheck.sch]
2021-09-15 Removed LaserFeedBinEmptyCheck Circuits.
    [LaserFeedBinEmptyCheck.kicad_pcb, LaserFeedBinEmptyCheck.sch]
2021-09-15 Add Waveshare Laser Sensor information.
2021-09-17 Add Pi4 board.
2021-09-17 Add Server Connections.
    [ServoHAT.fzz]
2021-09-18 Charger and Power Supply board completed.
    [ChargerAndPowerSupply.kicad_pcb, ChargerAndPowerSupply.sch]
2021-09-18 Minor update -- footprints and 3D shapes.
    [ChargerAndPowerSupply.kicad_pcb, ChargerAndPowerSupply.sch]
2021-09-20 Added additional dimensions.
    [ChargerAndPowerSupply.kicad_pcb]
2021-09-20 Added PS box and board 3D Models.
2024-08-11 Upgrade KiCAD files.
    [ChargerAndPowerSupply.kicad_pcb, ChargerAndPowerSupply.kicad_sch]
2024-08-13 Added additional breakout boards: rtc, load cell, power fail gpio.
    [ServoHAT.fzz]
2024-08-13 Add screen mounting bracket.
2024-08-13 BatteryBox completion: fingers for back, beams for top.
2024-08-13 Remove extra space for RPi touch screen, properly position beams for battery top.
2024-08-15 Add wire hole.
2024-08-15 Remove RPi, replace with ESP32-S3 Feather.
    [FeatherWingTFT.fzz, ServoHAT.fzz]
2024-08-15 Add Revision handling, create start screen, error message handling.
    [SmartCatFeederFirmware.ino]
2024-08-16 Updates to Readme (add links), move wire hole to accommodate a USB-C power cable, remove protoboard for power.
    [FeatherWingTFT.fzz]
2024-08-17 Working on the firmware.
    [partitions.csv]
2024-08-18 Add additional I2C boards.
2024-08-18 Add Clock and Force Sensor boaards.
2024-08-18 Add gear motor with mount plates.
2024-08-19 Gear Motor Mount for auger.
2024-08-19 Add agitator, with motor.
2024-08-21 Battery box updates.
2024-08-22 Add bowl support box screw holes.
2024-08-22 Add Power cord notches and back mounting beams.
2024-08-22 Finalize things, make first draft of panel cut sheets.
2024-08-23 Update readme: parts and materials list.
2024-08-24 Working on firmware.
    [partitions.csv]
2024-08-29 Completed Sensor code. (Need calibration!)
2024-08-30 Fix mounting hole problem with motor mount.
    [DFRobotGearMotor.py]
2024-09-01 Charger & PS bit drill and cut sheet. Readme updates.
2024-09-02 Finalize charger and ps.
    [ChargerAndPowerSupply.kicad_pcb]
2024-09-02 Tweaks to the Charger PS.
    [ChargerAndPowerSupply.kicad_sch]
2024-09-29 Small fix to Mechanical.cpp.
    [Mechanical.cpp]
2024-11-03 Build for a 4meg Feather.
    [partitions.csv]
2024-11-10 Revert "Build for a 4meg Feather."
    This reverts commit 0be278e8015b755209baf81524f555d6c02cfab5.
    [partitions.csv]
2024-11-10 Revert "nothing"
    This reverts commit 02002390b936040632b82b980f4eb395d3158ec8.
    [FoodBin.py]
2024-11-10 Provide targets for both 8Meg and 4Meg feathers.
    [partitions4M.csv, partitions8M.csv]
2024-11-26 Update auger mount holes and add auger mount.
2024-12-02 Add Wood BOM.
2024-12-05 Adjust battery box size.
2025-03-30 Add realistic Adafruit NAU7802.
    [AdafruitNAU7802.step]
2025-03-31 Final positioning Adafruit NAU7802. Enlarge wire hole.
2025-04-01 Add auger motor mount and motor.
2025-04-06 Redo panel cut sheets.
2025-04-15 Add nau7802_test -- needed for scale calibration.

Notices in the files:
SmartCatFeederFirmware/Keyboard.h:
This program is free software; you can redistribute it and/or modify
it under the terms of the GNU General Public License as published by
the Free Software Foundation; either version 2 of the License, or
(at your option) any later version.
